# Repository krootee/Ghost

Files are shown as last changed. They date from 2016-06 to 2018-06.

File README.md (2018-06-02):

# Ghost32

## Summary

Ghost32 is an autonomous car used for Folkrace robot competition. It uses a customized Losi 1/24-scale RTR 4WD Rally Car, and with a custom created PCB and various sensors. The "brain" of the car is an ESP32, and it is programmed using C++ and Mongoose OS.

This GitHub repository contains all relevant info for creating both hardware and software.

//More details about the project can be found on http://scalpel78.github.io/Ghost/

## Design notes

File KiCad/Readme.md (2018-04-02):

# Custom PCBs for Ghost

### PCBs

The bottom board, the GhostESP32, contains primarily the ESP32, a micro USB, an MPU-9250 and connectors.

The top board, the GhostSensorboard, contains primarily connectors for all the sensors, servos, power, startmodule, etc.

In the first revision it used the "Sick of Beige" 50x50 formfactor, but in the second revision this has been reduced to the slightly smaller 60x37 formfactor. Also, in the second revision the accelerometer/gyro and compass has been moved from the top board to the bottom board.

The electronics use two boards that are connected together using a Hirose FX8C connector.

There is a KiCad footprint for the Hirose FX8C-60 pin connector at: https://github.com/librespacefoundation/lsf-kicad-libs
and Sick-of-beige layout from https://github.com/TomKeddie/openscad-scripts

#### PCB - GhostESP32 (Microcontroller)

- [x] ESP-WROOM-32
- [x] MicroUSB
- [x] USB-to-UART (CP2102)
- [x] Power LED
- [x] Reset buttons for ESP-WROOM-32 (Reset)
- [x] Accelerometer/Gyro/Compass (MPU-9250)
- [x] Temperature (TMP102)
- [x] Connector for ESC/Motor
- [x] Connector for Steering servo

##### PCB - GhostSensorboard (Sensors and connectors)

- [x] I2C multipexer (TCA9548ARGER, 2pcs)
- [x] 16 connectors for I2C/IR sensors
- [ ] RGB LED
- [x] Connector for Startmodule
- [x] 3V3->5V level shifter (BSS138, see Sparkfun)

### Rev 6 (future)

#### Changes from Rev 5 to Rev 6
- [ ] Fix schematic for Q2. Pins 2 and 3 are switched.
- [ ] Use Sick-of-beige 60x37
- [ ] Change footprint for the 100uF capacitors to a bigger one?
- [ ] CP2102, remove the resistors for D- and D+
- [ ] Make sure the capacitors for MPU9250, CP2102 and ESP32 as placed close to the chip.
- [ ] CP2102, Add 4.7k pullup resistor to 3V3 on RST pin
- [ ] Replace CP2102 with CP2102N (faster, pin compatible, might require two more resistors)
- [ ] Make the CP210N bus-powered. No need to power it except when programming via USB. 
(see https://www.silabs.com/documents/public/application-notes/an976-cp2102-3-4-9-to-cp2102n-porting-guide.pdf)
Add 22.1k and 47.5k voltage divider.
- [ ] Replace slide switch with side switch, f.inst: 131-6979
- [ ] Smaller 3V3 regulator. How much current do we draw at most?
- [ ] Ability to measure battery voltage. (LTC2943CDD, 2366039)
- [ ] Change resistors and capacitors 0402 to 0603.
- [ ] Fix footprint for TMP102 on Ghost Sensorboard

### Rev 5 (18.mar 2018)

Formfactor: Sick-of-beige 70x43

#### Notes and workarounds
- The Q2 schematic is wrong. Pins 2 and 3 are switched.

#### New/Changes
- [x] Fix footprint for TMP102. Was too big on Rev4.
- [-] Figure out why MPU9250 doesn't work on Rev4.
- [-] Test I2C and IR sensors on Rev4
- [-] Test the NanoPixels on Rev4
- [-] Test the Motor/ESC pwm and Steering PWM
- [x] Change to the slightly bigger TCA9548 chip for easier soldering?
- [x] Minor layout adjustments; Move Q1, Q2, R1, R2 between CP2102 and ESP32
- [x] Minor layout adjustments; Move R15 and C12 closer to SW1 switch
- [x] Remove the NanoPixels
- [x] Change I2C to use pins 21 (SDA) and 22 (SCL)
- [x] Changed I2C pullups from 2k2 to 10k
- [x] Change PCB outline to a rectangle with rounded corners
- [x] Change MPU9250 to use I2C addr 0x69, instead of 0x68

### Rev 4 (aug 2017)

Formfactor: ca 63x43mm with "drone arms"
Had wrong footprint for TMP102.

- [x] Replace MPU6050 and HMC5883 with a MPU9250
- [x] Remove the TX/RX leds and BSS138 opamps
- [x] Remove the FX8 connectors
- [x] Breakout more of the pins from ESP32 to headers
- [x] Add JTAG header for ESP32
- [x] All resistors and capacitors should use footprint 0402.
- [x] Simplified components around reset switch
- [x] ESD protection (Farnell: 238-3318)
- [x] USB resistors on D+ and D-
- [x] Temperature sensor (TMP102)

### Rev 3 (never built??)

### Rev 2 (mars 2017)

Used formfactor Sick-of-beige 60x37

### Rev 1 (feb 2017)

Used formfactor Sick-of-beige 50x50.

### Other

Sensor board:
- [x] Add 5V regulator to go from VBAT to +5V
- [ ] Is the button on Sensorboard tall enough? (And do we need it?)
- [ ] Add motor driver (MCP8063? DRV10970?)
- [x] Put an LED in each corner of the Ghost Sensorboard.
- [ ] TCA9548ARGER has wrong footprint. Needs one with thermal GND pad.
- [x] Connect battery directly to top board
- [x] Add on/off switch (MFP106D, 807527)
- [ ] Remove the IR receiver?
- [x] (alt: replace IR sensor with one in stock)
- [x] All resistors and capacitors should use footprint 0402
- [x] Add NeoPixel nano RGB leds
- [x] Remove 8 of the IR sensors connectors + one I2C mux to save space

PCB
- [ ] Move motor and steering connectors away from ESP32 on other board
- [x] Typo. Steering is mistakenly written as Start.
- [x] 6mm keepout around the mounting holes, see Sick of Beiges specs
- [x] Ground area used by U12+P3 is not connected to rest of board!
- [ ] 4-layer board
- [x] Make sure no GND plane under MPU-9250, see https://github.com/kriswiner/MPU9250/issues/43

### Others

Arduino code for the Startmodule-remote is here:
http://p1r.se/startmodule/implement-yourself/#comment-1271

------- OLD BELOW ----------

### Schematic

- [x] Startmodule pins are wrong order!! Should be VCC, GND, Start
- [x] Add two buttons for ESP-WROOM-32
- [x] Change to TCA9548ARGER (smaller footprint than TCA9548APWR)
- [x] Change from 0805 to 0603 size for capacitors, resistors and leds.
- [x] Remove extra PWM pins?
- [x] Change pin headers around so that pin 1 (the square) is GND
- [x] Use resistor array for IR sensor resistors
- [x] Red LED is always on. Figure out why. (was Q1 pins switched)
- [x] Change the Q1 transistor schematic component to use Q_NPN_BEC
- [x] Add 6 pin header for FTDI Basic, for programming ESP8266
- [ ] Remove LED strip connector?
- [ ] Add connectors to breakout ESP-WROOM-32 pins?
- [ ] Micro USB for programming ESP-WROOM-32s
- [ ] CP2102 (or similar USB-to-UART bridge)
- [ ] Use the new 47uF or 100uF alu caps?
- [ ] Use the new resistor networks?

##### Board/layout
- [ ] Current size is about 90mm x 63mm. Try to reduce to "Sick of Beige" size 80x49 or 70x43.
- [ ] Make sure I have four mountingholes for acrylic cover
- [ ] Startmodule header needs indicator for direction
- [ ] Put all pin headers on the border of the PCB
- [ ] Fix missing trace between R7 and D3(red)
- [ ] Move LEDs to a more visible place. They are under Teensy USB now.
- [ ] Move MPU-6050 to the center of the board.
- [ ] Make sure antenna part of ESP-WROOM-32 sticks outside board.

#### Car
- [X] Fix wireposition on steering servo
- [ ] Change the steering servo
- [ ] Mount wheel encoder
- [ ] Create mount for IR sensors
- [ ] Figure out which battery to use
- [ ] Mount new motor.
- [ ] Figure out the gears for the motor

#### Other
- [ ] Draw acrylic cover for PCB in OpenSCAD
- [ ] Laser-cut an acrylic cover for PCB
- [ ] Use 0.1 ohm 1% 2W current sense resistor for the INA219. Find part at Farnell.

## Bill of materials / Partlist

### RC car

## PCB Features

### Teensy 3.1/3.2 (external)

Uses a standard Teensy 3.2 board from pjrc.com.

The Teensy is based around a MK20DX256VLH7, an ARM Cortex-M4 at 72MHz. It contains 2k EEPROM where the car's configuration is stored.

In later versions I'm planning on incorporating a custom Teensy directly into the PCB. If so, then I can remove the MIC5219-3.3, since the Teensy also comes with a 3.3V regulator.

### HM-11 bluetooth

Revision 1 has both Bluetooth and WiFi. This version is for determining if BT or WiFi is easiest to work with. Later versions will only have one of the two.

It is not allowed to remotely control the car during the Folkrace, but the BT/WiFi functionality is very useful during debugging and experimentation. It allows receiving telemetry data during racing, and makes it easy to change configuration without reprogramming entire Teensy.

### ESP8266 WiFi

An ESP-12E.

The ESP8266 contains an 80MHz 32-bit RISC CPU with 16 GPIOs, SPI, UART and I2C. In itself it is a powerful chip, and could potentially make the Teensy redundant.

Information gathered from (http://www.esp8266.com/wiki/doku.php?id=esp8266-module-family).
Pin 1, RST: Connect to switch to GND in order to reset.
Pin 3, EN : Connect to 3.3V to enable.
Pin 8, VCC: To 3.3V
Pin 15,GND: To GND
Pin 16,GPIO15: Need to connect to GND.

### MPU-6050 (accelerometer and gyro)

In order to detect movement there is an MPU6050 MEMS motion tracking device with accelerometer and gyro, and an HMC5883 compass.

To interface the MPU-6050 I'm using code from Jeff Rowberg (https://github.com/jrowberg/i2cdevlib/tree/master/Arduino/MPU6050)

 Alternatively I'm going to use FreeIMU (http://www.varesano.net/projects/hardware/FreeIMU).

 Future revisions might replace this with a MPU-9250.

### HMC5883 (compass)

The compass is a slave-I2C device where the MPU-6050 is the master. FreeIMU uses these two components together.

### I2C multiplexer and 8 IR sensors

Since the I2C IR sensors I'm using all have the same I2C address I need to multiplex between them using an I2C mux.

The multiplexer is an TCA9548APWR with eight channels.
In Rev 1 I'm using a multiplexer with footprint TSSOP (7.8 x 4.4 mm). In future revisions I'm considering changing to TCA9548ARGER which has a VQFN footprint (4 x 4 mm). They both have 24 pins, but NOT the same pin configuration.

The IR sensors are eight Sharp GP2Y0E02B, which uses I2C. It has range 4-50cm.

### Current sensor

An INA219BIDR is used for sensing current usage. Measures current flow from the battery connected. Device is controlled by I2C. Adafruit has an Arduino library for the INA219.

The sensor can sense up to 3.2A in 0.8mA steps.

Arduino code: /Arduino/CurrentSensor/CurrentSensor.ino

### Voltage regulator

The 7.4V Li-Po battery is connected to the XC-10A ESC, and it provides regulated +5V/1A to the PCB. The Hobbyking XC-10A accepts from 3v-13V, so I could potentially use an 11.1V LiPo.

On the PCB is a MIC5219-3.3YM5 voltage regulator for providing 3.3V. It has a max output of 500mA.

The Teensy also has built in 3.3V regulator. It can supply 500mA. Currently not used.

### Toggle LEDs

There are two leds, one red and one green, which can be toggled from Teensy. Only one of them can be active at any given time.

When Teensy pin 2 is HIGH the transistor turns on, and the Green led lights up. When pin 2 is LOW the Red LED lights up.

NB, in Rev 1 the schematic part for the transistor is wrong. It has switched Collector and Emitter, leaving the red led on always. Fixed in Rev 2.

### GPIOs
#### Startmodule

For connecting a Startmodule from http://www.startmodule.com/.

NB - Rev 1 had wrong pinout! Fixed in Rev 2.

#### Steering servo

For controlling a SG-90 or similar microservo for steering. I'm using Losi part LOSB0814, which is a three-pin replacement servo with servo saver.

  1. PWM control signal to Teensy pin 4.
  2. +5V
  3. GND

#### Motor

A 3 pin header for connecting an Electronic Speed Control (ESC). I'm using the HobbyKing XC-10A esc.

  1. PWM control signal to Teensy pin 3.
  2. Power from the Li-Po battery. Used to power entire PCB.
  3. Ground

Arduino code: Arduino\MotorHobbykingXC10AESC\MotorHobbykingXC10AESC.ino

#### General purpose button

A generic purpose switch, usage to be determined by user. Use INPUT_PULLUP when setting pinMode(pin, INPUT_PULLUP).

#### General purpose PWM connector

Usage to be defined by user
  1. PWM control signal to Teensy pin 16.
  2. +5V
  3. GND

#### Wheel encoder

Either GP1A51HRJOOF or KTIR0611S photo interrupter. Used to measure rate of spinning for the main drive shaft.

## Current consumption

If I need more than 500mA on the 3.3V rail I might go for å AMS1117 or similar, which can handle 1A.

(todo)

## Further research

https://github.com/guyc/RC5
https://github.com/pinkeen/avr-rc5
http://clearwater.com.au/code/rc5

https://github.com/platisd/AndroidCar/

https://github.com/esp8266/Arduino/blob/master/doc/reference.md

http://control.ee.ethz.ch/index.cgi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

Check out the USB driver chip CH340.

https://esp-idf.readthedocs.io/

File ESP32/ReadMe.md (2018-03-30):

# ESP32 / ESP-WROOM-32

This page contains my notes about programming the ESP-WROOM-32 module.

The primary sourcecode for the Ghost-folkracer car is in the /Folkracer directory.
All code for testing individual parts of the car can be found in the /TestPrograms dir.

## Using Arduino IDE

To program the board using the Arduino IDE first follow the installation instructions at https://github.com/espressif/arduino-esp32.

In Arduino IDE choose the board called 'ESP32 Dev Module'.
The blinky-led is on pin 23.

## Using C++ and ESP-IDF

Documentation and installation guide for ESP-IDF can be found at: https://esp-idf.readthedocs.io

### Prerequisites (Ubuntu/Linux Mint)

Perform installation Step 0 to Step 2 from the documentation link above.

In addition, add this to ~/.bashrc as well (from Step 4):

    export IDF_PATH=~/esp/esp-idf

### Flashing

Go to the /Ghost/ESP32/Folkracer directory, and run

    make flash (flashes app, bootloader and partition table)

or

    make app-flash (flashes just the app)

or

    make all flash monitor (builds everything, flashes and starts the monitor with one command)

To close the 'monitor' use keys Ctrl+] (which is Ctrl+AltGr+9 on Norwegian keyboards).

### Performance

    make -j5 (performs the build with parallell threads)

### Configuring Eclipse

When starting Eclipse, set ~/GIT/Ghost/ESP32 as the workspace folder.

On properties for the project, go to "C/C++ Build", and uncheck "Use default build command".
Go to Environment, and add IDF_PATH = ~/esp/esp-idf
Go to "C/C++ General"->"Paths and Symbols", select "GNU C", click Add..., and add these:

    ${IDF_PATH}/components/esp32/include
    ${IDF_PATH}/components/newlib/include
    ${IDF_PATH}/components/freertos/include
    ${IDF_PATH}/components/nvs_flash/include
    ${IDF_PATH}/components/driver/include
    ${IDF_PATH}/components/log/include

and lastly

    /myapp/build/include (with the "Is a workspace path" checkbox ticked, and correct appname)

### Using OTA

First, make sure the ota.bin firmware has been deployed using USB cable.

    cd ~/esp/esp-idf/examples/system/ota
    make menuconfig
        configure correct SSID, password, IP to webserver, and .bin file to download.
    make flash

Set up a local HTTP webserver in the /build directory of the application to deploy Using

    python2 -m SimpleHTTPServer 8070

Now, rebuild the project we want to deploy, so that the .bin file gets created/updated.
Press Reset button on ESP to make it restart, download new image and reflash itself.

### Connecting serial

Install Minicom

    sudo apt-get install minicom

and to use

    minicom --device /dev/ttyUSB0

or you can use

    make monitor

Quit it using Ctrl+] (which is Ctrl+AltGr+9)

### Troubleshooting

##### Unable to flash via USB - permission denied

When running "make app-flash" or similar you get error saying permission denied to the USB device.

This can be fixed by adding the current Linux-user to the 'dialout' group.

    sudo usermod -a -G dialout $USER

Reboot the machine afterwards.

##### OTA fails
https://github.com/espressif/esp-idf/issues/231

##### TODO

- separate task_actuators into task_motor and task_steering, and write to two separate queues from task_drivecomputer.

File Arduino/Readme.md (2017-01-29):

# Arduino code

### Isolated sketches for testing

Most of the code in this directory are small Arduino sketches focused on just testing and verifying one particular piece of the puzzle. There is one for the IR sensors, one for the motors, one for the startmodule etc. This makes it easy to validate that a particular piece of hardware works.

### Main program

The code in the Ghost folder is the main program for the RC car. It contains the full program for running the RC car.

### Path planning

Middle Path (MP) and Minimum Curvature Path (MCP) - see http://www.aueb.gr/users/ion/docs/stavrinos_bsc_thesis.pdf

##### Further research

D* lite

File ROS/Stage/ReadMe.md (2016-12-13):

## Using Player/Stage to simulate

These files are used by Player/Stage to run robot simulation.

### Install

On Ubuntu 16.04 install ROS using ´´´sudo apt-get install ros-kinetic-desktop-full´´´. That should also bring in the ros-kinetic-stage application.

You _might_ need to add this to ~.bashrc

export LD_LIBRARY_PATH=/usr/local/lib64:$LD_LIBRARY_PATH}
export PKG_CONFIG_PATH=/usr/local/lib64/pkgconfig:$PKG_CONFIG_PATH}

Then start simulation by running

´´´stage gothenburg.world´´´

NB - I was unable to get Player working on Ubuntu 16.04. I tried downloading the current snapshot from https://sourceforge.net/p/playerstage/svn/HEAD/tree/, and built it, but never managed to get everything working.

### Links
http://rtv.github.io/Stage/
and
http://playerstage.sourceforge.net/index.php?src=stage
and
http://player-stage-manual.readthedocs.io/

http://askubuntu.com/questions/859110/install-package-robot-player-on-ubuntu-16-04

http://answers.ros.org/question/249570/gazebo-or-rviz/

https://discourse.ros.org/t/using-ros-for-simulating-autonomous-rc-cars/924

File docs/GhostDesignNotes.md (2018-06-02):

# Ghost Design Notes

*These design notes are scribbled down as I'm doing research for my autonomous Folkrace cars.*

*I'm trying out several different options for the software, so there are code for both Arduino, FreeRTOS and Mongoose OS. The last one is my main focus now.

## Sensors

* Either up to 8 or up to 16 distance sensors. Hopefully 8 will be enough.
* Compass
* Accelerometer/Gyro
* Wheel encoder

___
## Logic

The math in the car will use Vectors as the main means of calculations. 
Each distance sensor is one vector where the direction is constant (set by how it is mounted on the car), and a variable amplitude (the distance measured). 

By combining two vectors pointing to the same side wall, the angle of the car vs the wall can be calculated using vector math.

In addition, I'll use a vector to describe the desired forward motion. The vector will indicate the direction and speed the car should go.

The speed of the car will be affected by the steering angle. When going straight forward the car will move at a higher speed, than when turning. A sharp turn should be done at a very low speed.

The minimal speed the car can go must be identified.

Using a sensor to measure the rotation of the driveshaft, Odometry can be used.

### Car and sensorssetup

Each sensor will have a constant offset from a common point of the car, describing how far in the X and Y direction the sensor is from the zero-point.

The Zero-point is in the middle between the two rear tires.

The Tread-size is the distance between the two rear wheels, and the Wheelbase is the distance between the rear and front wheels. [1]

Overall car state:

```
{
  env: {
    leftwalll: 32,
    rightwall: 29,
    incline: 3
  },
  pose: {
    velocity: 180,
    direction: 230,
    steering: 76,
    motorspeed: 102,
    odometer: 79
  },
  sensors: {
    irsensor1: true,
    irsensor2: true,
    irsensor3: true,
    irsensor4: false,
    irsensor5: true,
    odometer: true,
    compass: true,
    startmodule: true,
    accelerometer: true
  }
}
```

The modes can be: 'waiting', 'driving', 'stopped'.

Heading is degrees in [0-360].

Speed is in centimeters pr second. It is the actual speed, not the desired speed.
___

## Sensor Fusion

## Math
For Matrix math - http://arma.sourceforge.net. Remains to figure out how to use it from ESP32.

https://www.sciencedirect.com/science/article/pii/S1877050917301473

# Sources
[1] https://www.youtube.com/watch?v=i6uBwudwA5o

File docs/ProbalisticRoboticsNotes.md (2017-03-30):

# Notes from Probabilistic Robotics book
Book authors: Sebastian Thrun, Wolfram Burgard, Dieter Fox

Notes: Frode Lillerud, march/april 2017

# Chap 1 - Basics

### 1.3
Probabilistic robotics tend to be more robust than model-based motion planning techniques or reactive behavior-based approaches.

(My Arduino based folkracer is mostly "reactive behavior based", since it just reacts to the IR sensor inputs.)

Probabilistic robotics is have weaker requirements on the accuracy of the robot's model, and the accuracy of the sensors.

Two disadvantages are that PR have a higher *computational complexity*, and there is *a need to approximate*.

# Chap 2 - Recursive State Estimation

### 2.1

At the core of PR is the idea of *estimating state from sensor data*. State estimation seeks to recover state variables from the data.

### 2.2
``p(X=x)`` where X is the discrete set of all possible values, and x  is a specific value. This is commonly abbreviated as p(x).

#### 2.3.1 - State

State is denoted by ``x``, and ``xt`` is the state at time t.

Pose: Location and orientation relative to a global coordinate frame. Pose includes variables for the *configuration of the robots actuators*.

Robot *velocity* and *the joints velocities* are commonly referred to as *dynamic state*.

#### 2.3.2 - Environment Interaction

*Environment measurement data* is information gathered via cameras, sensors, etc.

*Control data* can be *velocity*.

Measurement and control; Measurement gives the robot MORE information about the environment, while control (moving actuators etc.) leaves the robot with LESS information about the environment.

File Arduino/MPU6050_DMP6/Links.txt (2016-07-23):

http://diyhacking.com/arduino-mpu-6050-imu-sensor-tutorial/

https://github.com/jrowberg/i2cdevlib/tree/master/Arduino/MPU6050

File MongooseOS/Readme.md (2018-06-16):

# Mongoose OS

See https://www.mongoose-os.com and https://forum.mongoose-os.com

## Setting up programming environment

### Basic - getting started
    1) Download mos.exe into f.instance C:\MOS
    2) Put that directory into PATH
    3) Create a project folder

      cd MOS
      mkdir MOSprojectABC
      cd MOSprojectABC
      mos init

    4) In mos.yml, add the following line

      platform: esp32

    5) After making changes to the generated src/main.c file use this to build and flash to board.

      mos build
      mos flash
      mos console

    6) Connect to WIFI using

      mos wifi SSID password

Note; for Ghost32 PCB revisions 1-5 the maximum baudrate when flashing is 921600bps (from CP2102).
Planning to use CP2102N in revision 6+, which will give maximum baudrate 3Mbps.

      mos build --clean | grep "error"
      mos flash --esp-baud-rate 921600
      mos console

### Using Visual Studio Code
Once you've got the basic setup above working you should also consider configuring VS.CODE to have a better programming experience.

    1) Install Visual Studio Code
    Go to https://code.visualstudio.com

    2) Add the C/C++ extension
    3) Add the tasks.json file below:

    (content of tasks.json):
    {
    "version": "0.1.0",
    "command": "mos",
    "args": ["build"],
    "problemMatcher": {
        "owner": "cpp",
        "fileLocation": ["relative", "${workspaceRoot}"],
        "pattern": {
            "regexp": "^(.*):(\\d+):(\\d+):\\s+(warning|error):\\s+(.*)$",
            "file": 1,
            "line": 2,
            "column": 3,
            "severity": 4,
            "message": 5
        }
      }
    }

    4) Clone the GIT repository (to get the headers for intellisense)

    cd C:\MOS
    git clone https://github.com/cesanta/mongoose-os.git

    5) Add Include Dirs in VS.CODE

    In your main.c file, click on one of the "#include" lines that have a red squiggly underneath. Then click yellow lightbulb to the left, and choose "Add include path to settings".

    Under the Win32 section in the c_cpp_properties.json file that appears, add "C:/MOS/mongoose-os" to both "includePath", and to "path". Notice that it uses forward slash.

    Go back to main.c and observe that the red squiggly lines are gone. Type in f.instance 'mgos_gpio' to observe that you have intellisense now.

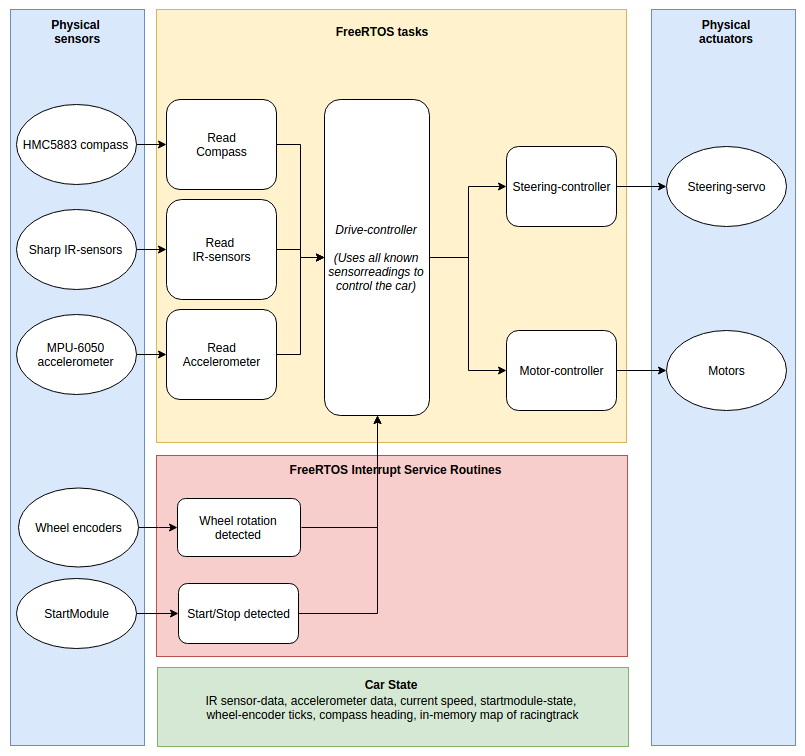
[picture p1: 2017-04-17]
docs/Architecture.png

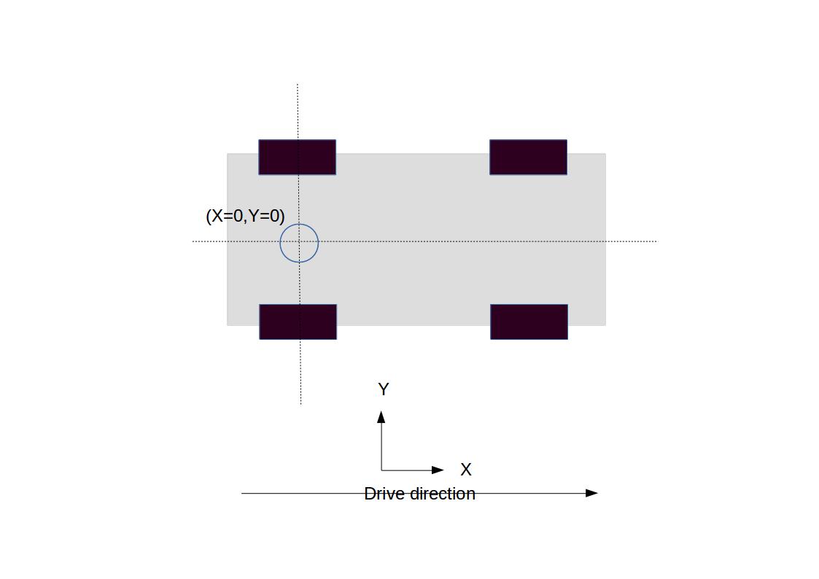
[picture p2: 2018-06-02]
docs/CoordinateSystem.jpg

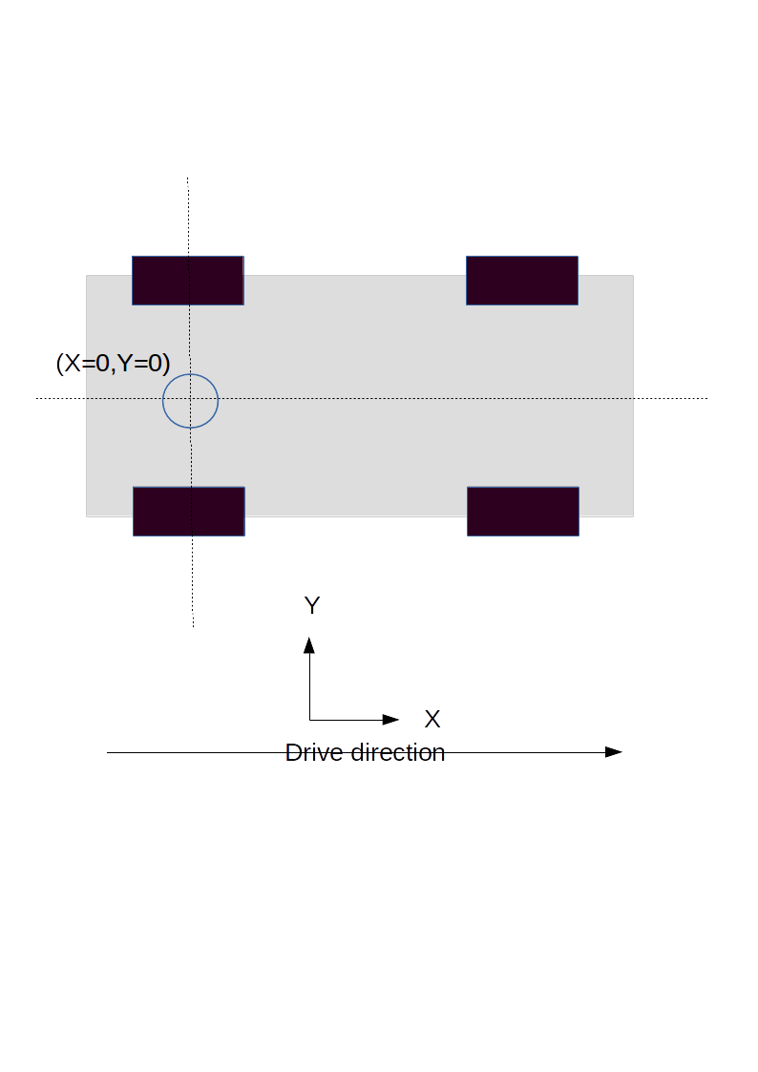
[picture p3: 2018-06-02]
docs/CoordinateSystem.png

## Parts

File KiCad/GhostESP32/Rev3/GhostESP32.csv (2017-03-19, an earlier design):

Id | Designator | Package | Quantity | Designation | Supplier and ref
1 | SW1 | SlideSwitchSpringReturn | 1 | SW_SPDT
2 | C1,C2,C3,C7 | C_0603 | 4 | 10uF
3 | C4 | C_0603 | 1 | 100uF
4 | C5,C8,C11 | C_0603 | 3 | 0.1uF
5 | C6 | C_0603 | 1 | 1uF
6 | C9,C10 | C_0603 | 2 | 1nF
7 | D1 | LED_0603 | 1 | RED LED
8 | D2 | LED_0603 | 1 | LED
9 | D3 | LED_0603 | 1 | RXLED
10 | D4 | LED_0603 | 1 | TXLED
11 | D5 | D_SMA_Standard | 1 | SSA33L Schottky
12 | J1 | hrs-fx8c-40p-sv | 1 | CONN_02X20
13 | P1 | USB_Micro-B | 1 | USB_OTG
14 | Q1,Q2,Q3 | SOT-23 | 3 | Q_NPN_BEC
15 | R1 | R_0603 | 1 | 2K
16 | R2 | R_0603 | 1 | 390
17 | R3,R4,R11 | R_0603 | 3 | 12K
18 | R5,R6 | R_0603 | 2 | 1k
19 | R7,R10 | R_0603 | 2 | 470
20 | U1 | SOIC-8_3.9x4.9mm_Pitch1.27mm | 1 | LM358
21 | U2 | SOT-223-3Lead_TabPin2 | 1 | NCP1117ST33T3G
22 | U3 | QFN-28-1EP_5x5mm_Pitch0.5mm | 1 | CP2102
23 | U4 | ESP32-WROOM | 1 | ESP-WROOM-32
24 | C12 | C_0603 | 1 | 10nF
25 | C13 | C_0603 | 1 | 2.2nF
26 | C14 | C_0603 | 1 | 0.22uF
27 | C15 | C_0603 | 1 | 4.7uF
28 | R8,R9 | R_0603 | 2 | 2k2
29 | U5 | QFN-24-1EP_4x4mm_Pitch0.5mm | 1 | MPU-6050
30 | U6 | QFN-16-1EP_3x3mm_Pitch0.5mm | 1 | HMC5883
31 | R12 | R_0603 | 1 | 10k

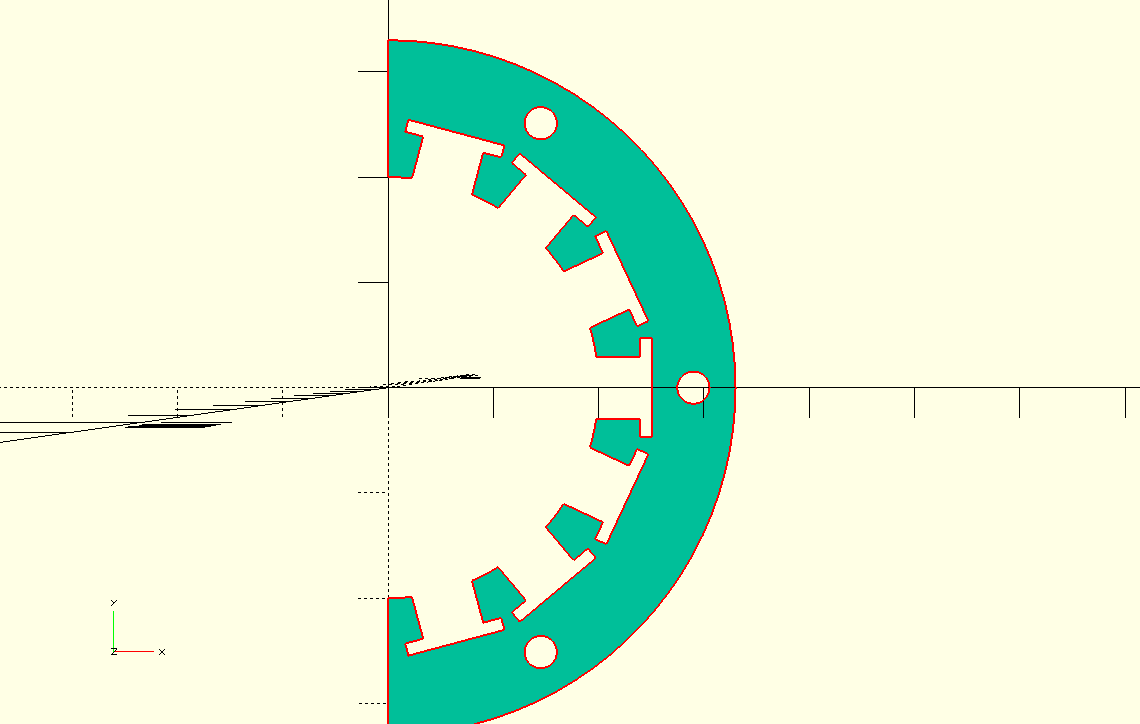
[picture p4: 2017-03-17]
Parts Lasercut/SensorFrame_WithHoles.png

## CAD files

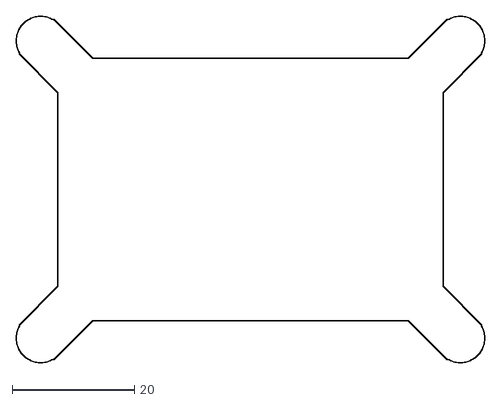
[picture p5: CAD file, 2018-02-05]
KiCad/OpenSCAD PCB/PCB-outline-rev4.dxf
76.7 x 56.7

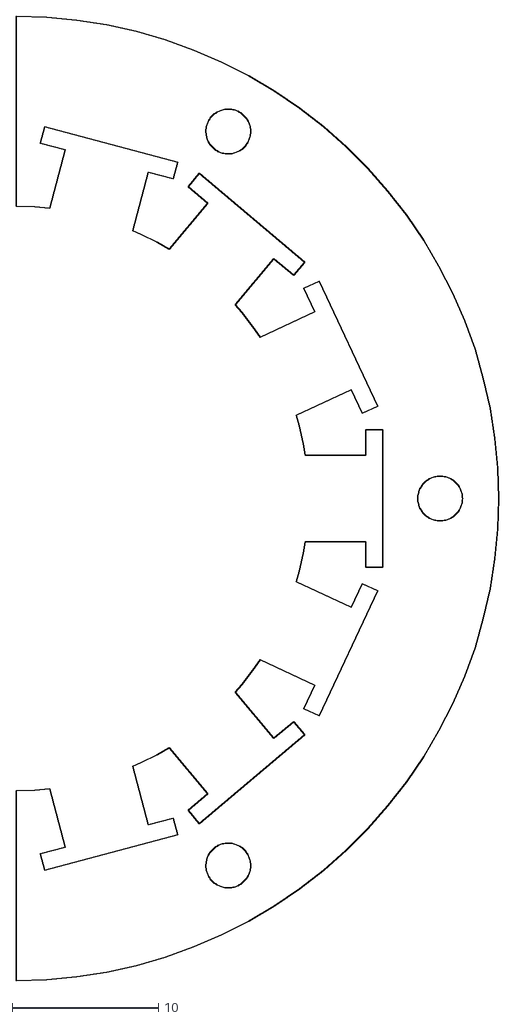
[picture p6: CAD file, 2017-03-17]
Parts Lasercut/SensorFrame_WithHolesV2.dxf
33.0 x 66.0

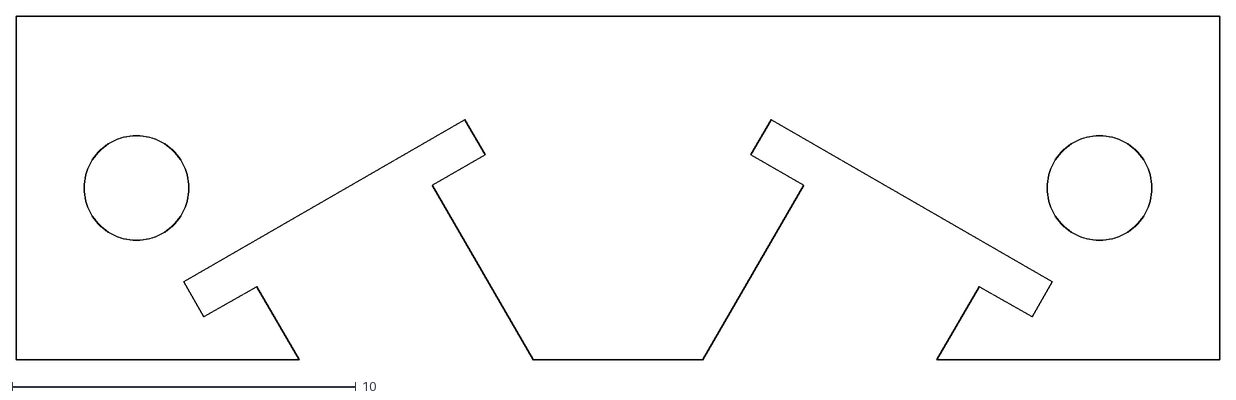
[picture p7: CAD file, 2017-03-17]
Parts Lasercut/MiniSensorHolder.dxf
35.0 x 10.0

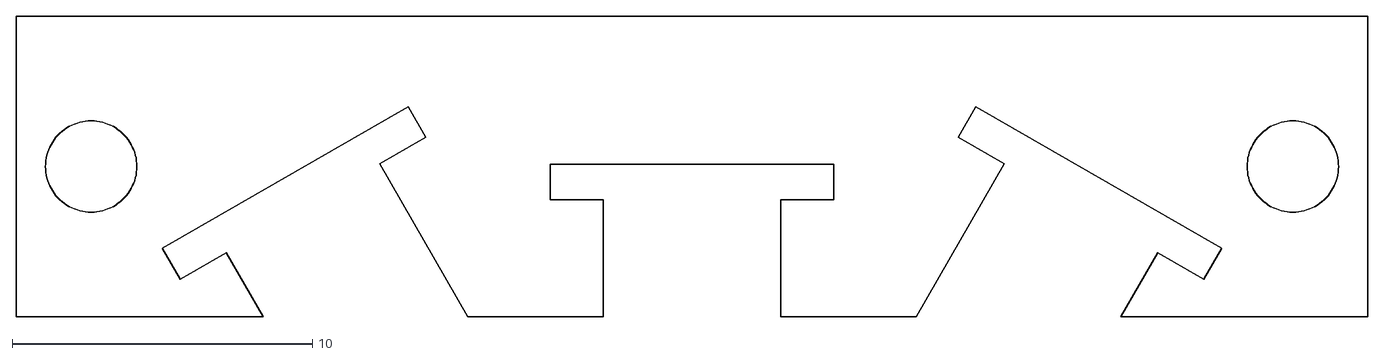
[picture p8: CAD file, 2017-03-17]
Parts Lasercut/ThreeSensors.dxf
45.0 x 10.0

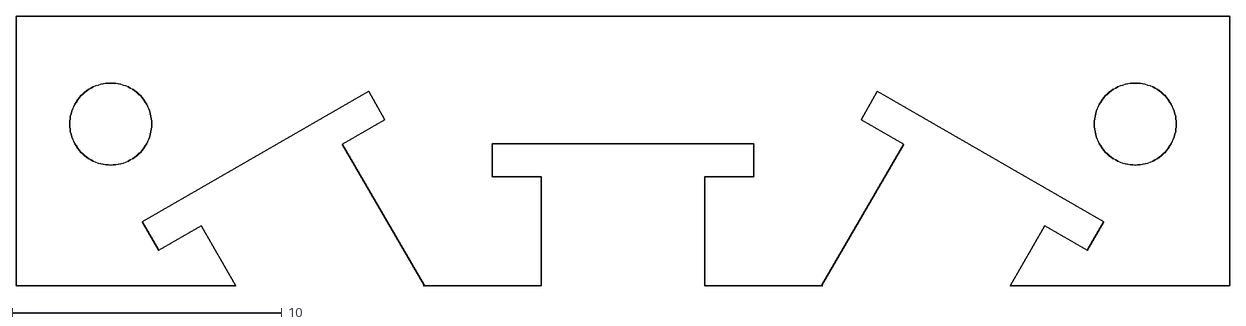
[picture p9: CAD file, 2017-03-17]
Parts Lasercut/ThreeSensorsV2.dxf
45.0 x 10.0

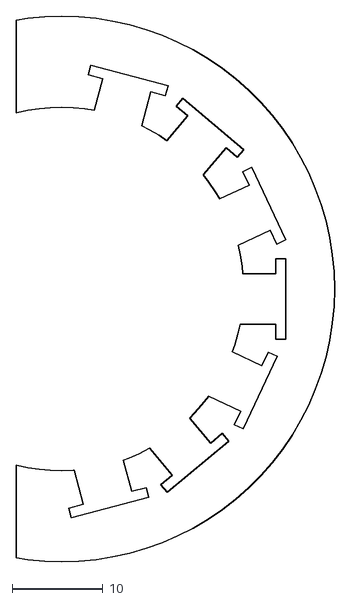
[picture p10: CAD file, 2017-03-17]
Parts Lasercut/SensorFrame.dxf
35.0 x 60.0

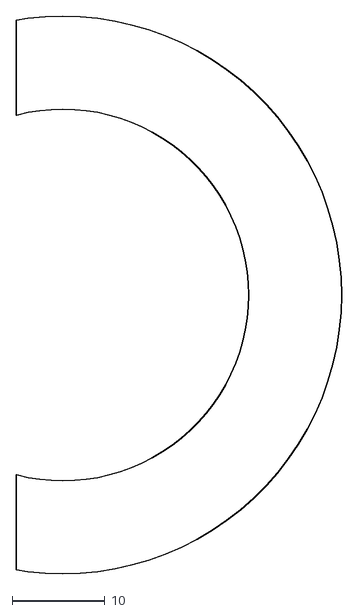
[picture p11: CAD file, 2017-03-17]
Parts Lasercut/SensorFrame_withoutHoles.dxf
35.0 x 60.0

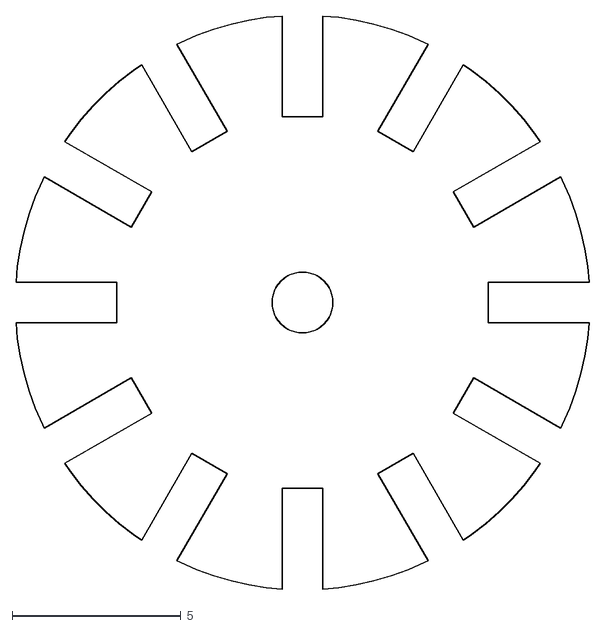
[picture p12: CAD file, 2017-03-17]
Parts Lasercut/EncoderDisc.dxf
17.0 x 17.0

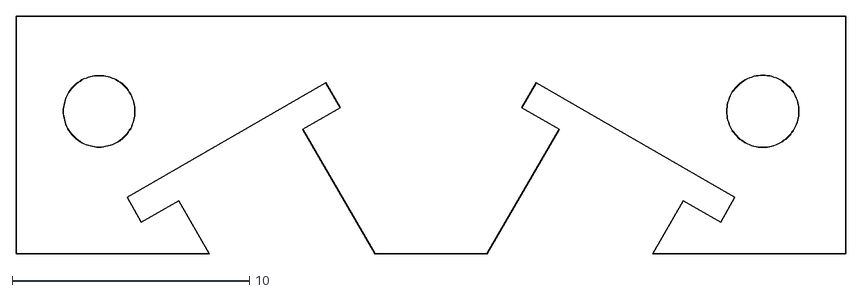
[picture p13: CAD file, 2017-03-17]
Parts Lasercut/MiniSensorHolderV2.dxf
35.0 x 10.0

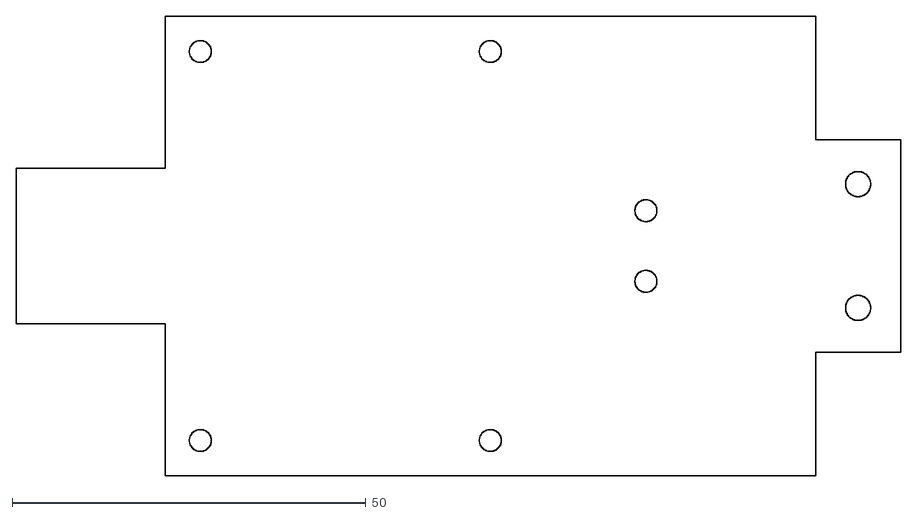
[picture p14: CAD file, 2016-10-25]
Parts Lasercut/PCB-mount.dxf
125.0 x 65.0

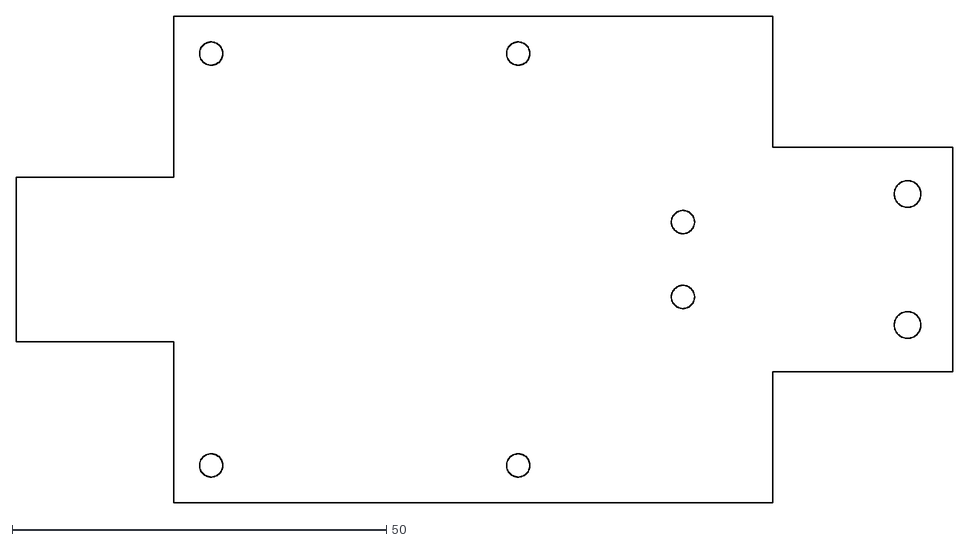
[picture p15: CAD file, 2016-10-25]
Parts Lasercut/PCB-mount-v2.dxf
125.0 x 65.0

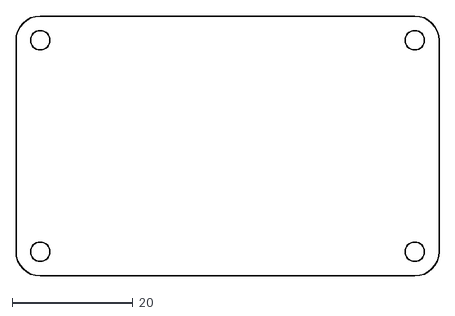
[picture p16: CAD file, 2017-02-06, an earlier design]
KiCad/GhostESP32/Rev3/DP7043.dxf
70.0 x 43.0

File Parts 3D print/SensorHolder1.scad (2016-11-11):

union() {
    linear_extrude(height=20) 
    {
        translate([0,0,0]) square([10,5]);
        translate([0,0,0]) rotate(90) square([15,5]);
        translate([45,15,0]) rotate(90) square([5,50]);
        translate([45,0,0]) square([5,20]);
        translate([35, 0,0]) square([10,5]);
    }
    translate([-10,-20,0]) cube([65,40,2]);
    #cylinder(size=20, height=20);
}

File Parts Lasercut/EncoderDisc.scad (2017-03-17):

$fn = 100;

projection(cut=false)
difference() {
    
    translate([0,0,0.5]) cylinder(r = 8.5, h=0.1);
    cylinder(r=0.9);
    for (a = [0 : 30 : 360])
        rotate(a) translate([7, 0, 1]) cube([3,1.2,1], center=true); //cylinder(r=0.8);
}

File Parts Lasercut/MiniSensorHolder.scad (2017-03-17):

$fn=100;

module sensor()
{
    width = 8;
    scaleFactor = 1.21;
    
    scale(scaleFactor)
    translate([0,-2.5,-5])
    union() {
        cube([5.5,5,10]);
        translate([5,-1.5,-3]) cube([1,width,19]);
    }
}


projection(cut=false)
difference() 
{
    cube([35, 10, 3], center=true);
    translate([5,-6.5,0]) rotate(60) sensor();
    mirror() translate([5,-6.5,0]) rotate(60) sensor();
    //translate([-5, -6.5, 0]) rotate(120) sensor();
    
    translate([14,1,-2]) cylinder(r=1.52, h=10);
    mirror() translate([14,1,-2]) cylinder(r=1.51, h=10);
}

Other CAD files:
Parts Lasercut/SensorFrame.scad
KiCad/OpenSCAD PCB/PCB-outline-rev4.scad
Parts Lasercut/PCB-mount.scad
Parts Lasercut/PCB-top-plate.scad
Parts Lasercut/ThreeSensors.scad

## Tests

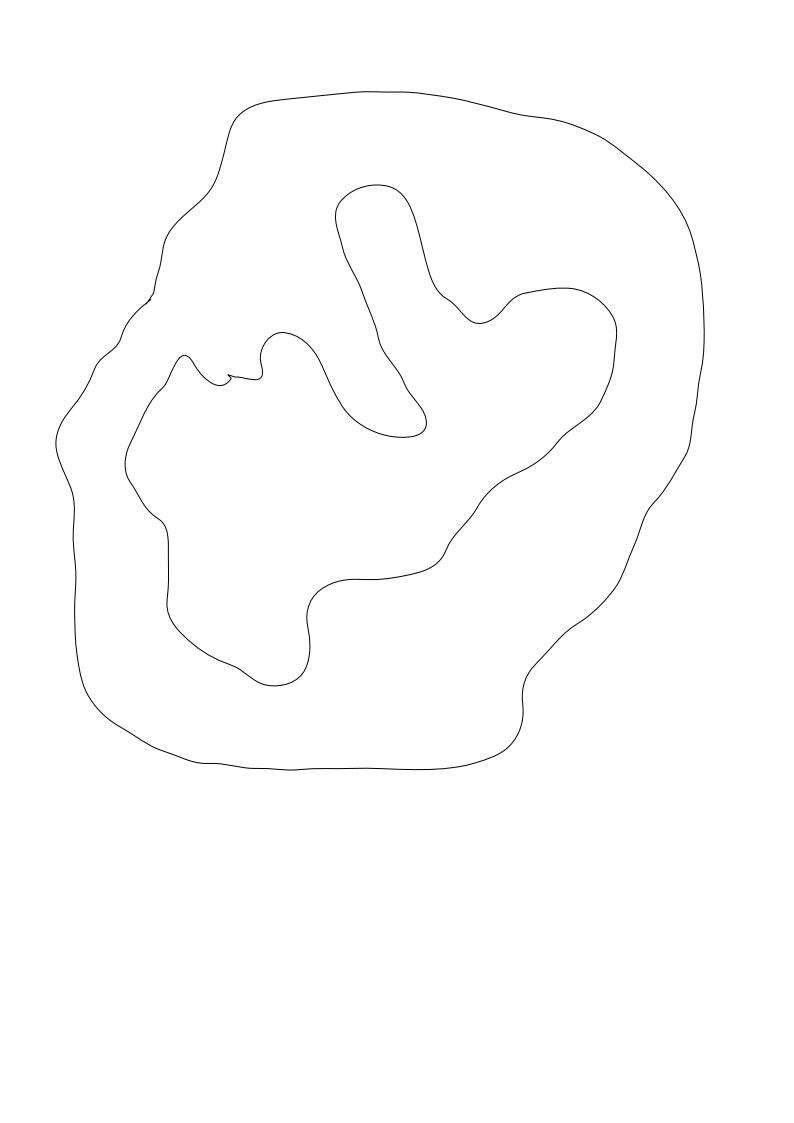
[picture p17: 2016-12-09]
ROS/Stage/bitmaps/test.bmp

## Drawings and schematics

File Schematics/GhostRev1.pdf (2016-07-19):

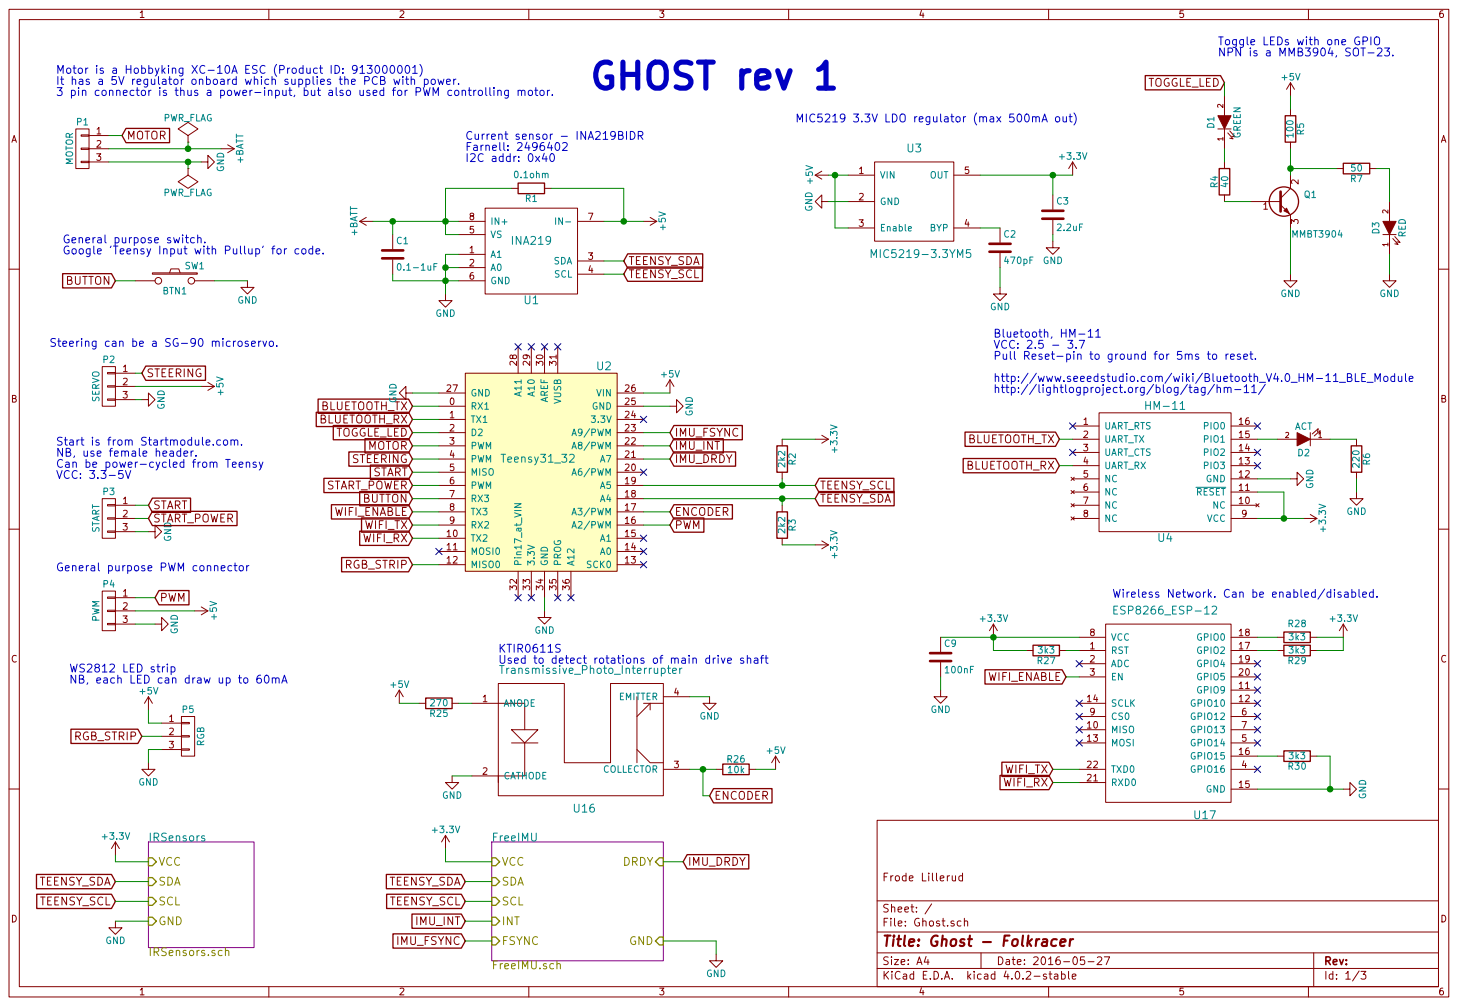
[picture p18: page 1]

Toggle LEDs with one GPIO

Motor is a Hobbyking XC-10A ESC (Product ID: 913000001)
It has a 5V regulator onboard which supplies the PCB with power.
3 pin connector is thus a power-input, but also used for PWM controlling motor.

MIC5219 3.3V LDO regulator (max 500mA out) +5V GND

General purpose switch.
Google 'Teensy Input with Pullup' for code. GND
GND WS2812 LED strip
BUTTON

Bluetooth, HM-11
VCC: 2.5 - 3.7
Pull Reset-pin to ground for 5ms to reset.
http://www.seeedstudio.com/wiki/Bluetooth_V4.0_HM-11_BLE_Module

Steering can be a SG-90 microservo.

Start is from Startmodule.com.
NB, use female header.
Can be power-cycled from Teensy

NB, each LED can draw up to 60mA

Id: 1/3 Title: Ghost - Folkracer File: Ghost.sch Sheet: / Frode Lillerud FreeIMU
FreeIMU.sch VCC
SDA
SCL
INT

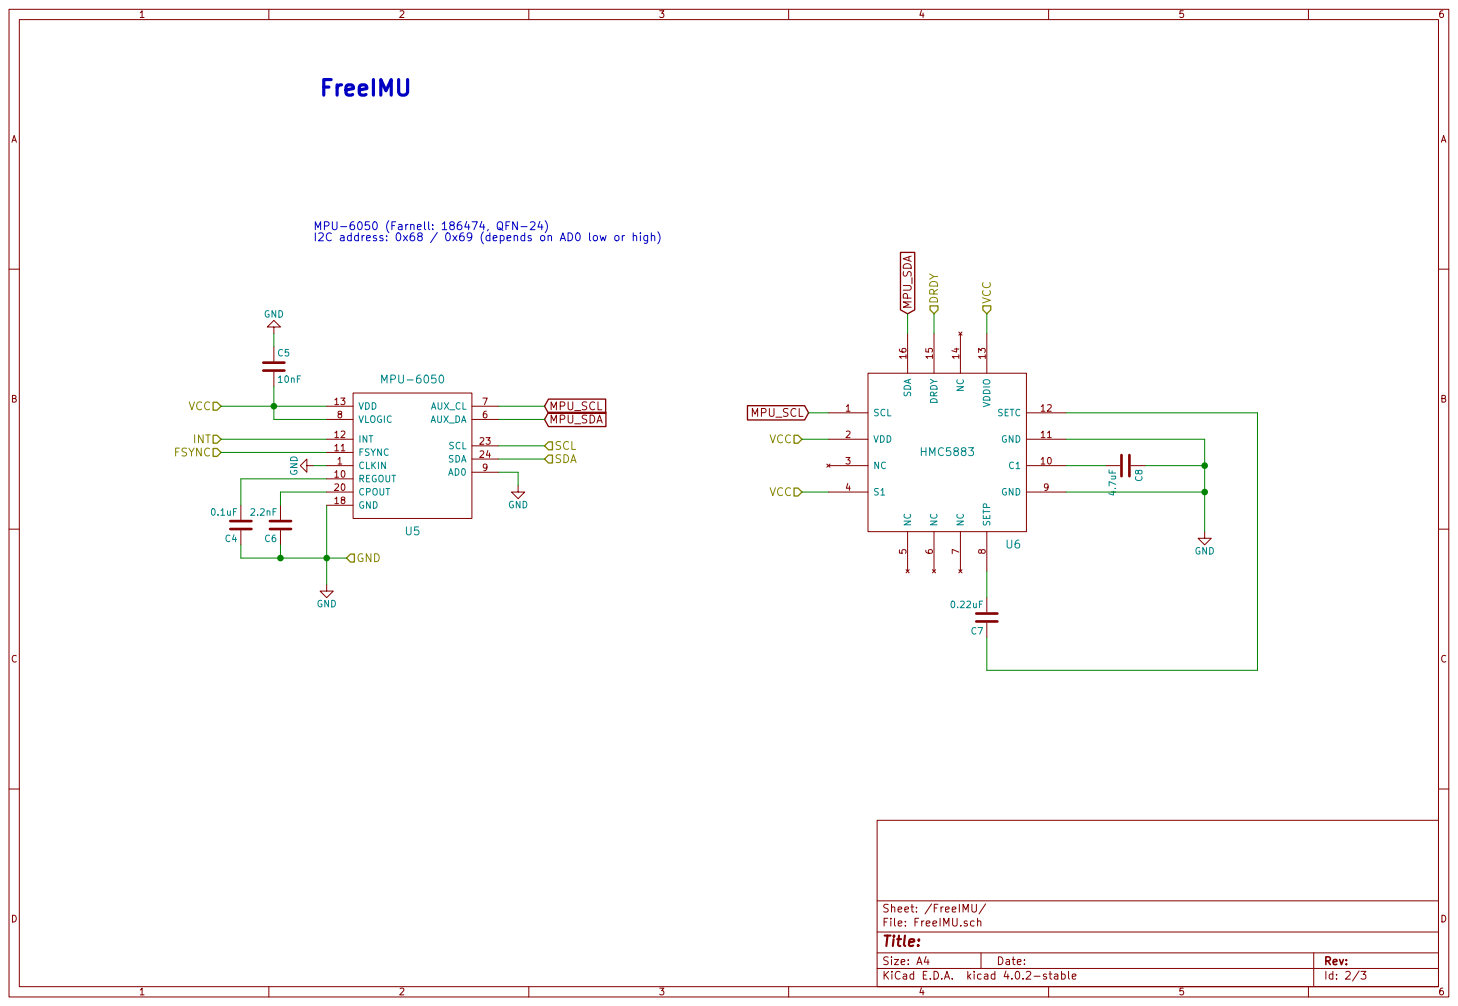
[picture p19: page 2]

MPU-6050 (Farnell: 186474, QFN-24)
I2C address: 0x68 / 0x69 (depends on AD0 low or high)

8 GND 9 C1 10 GND 11 SETC 12 VDDIO 13 NC 14 DRDY 15 SDA 16 U6 HMC5883

Id: 2/3 Title: File: FreeIMU.sch Sheet: /FreeIMU/

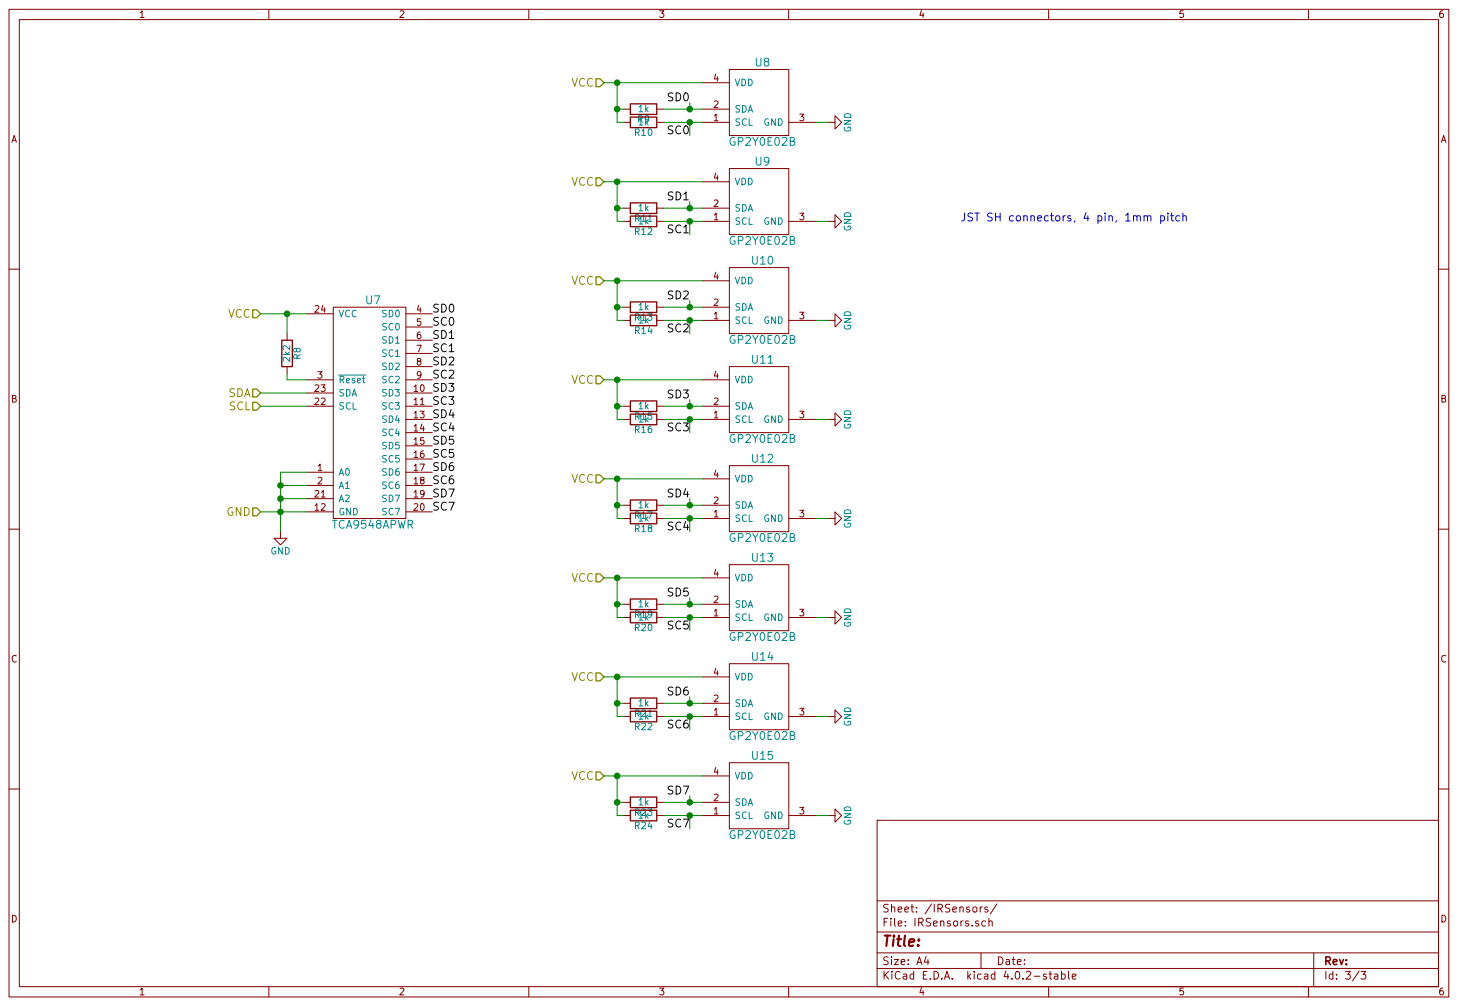
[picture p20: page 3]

JST SH connectors, 4 pin, 1mm pitch

Id: 3/3 Title: File: IRSensors.sch Sheet: /IRSensors/

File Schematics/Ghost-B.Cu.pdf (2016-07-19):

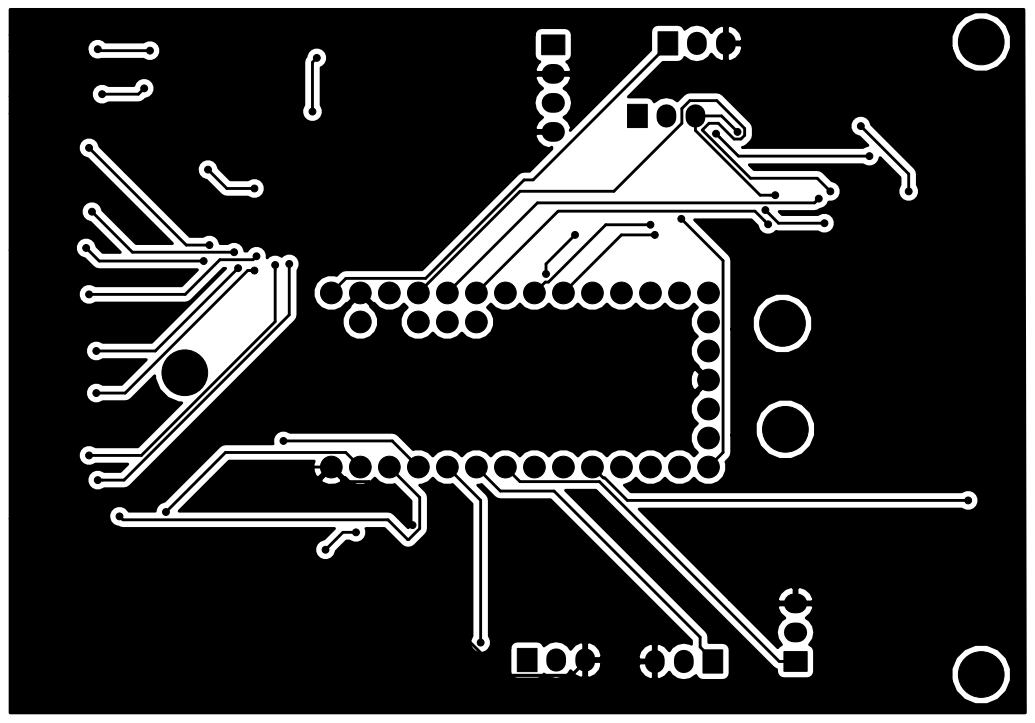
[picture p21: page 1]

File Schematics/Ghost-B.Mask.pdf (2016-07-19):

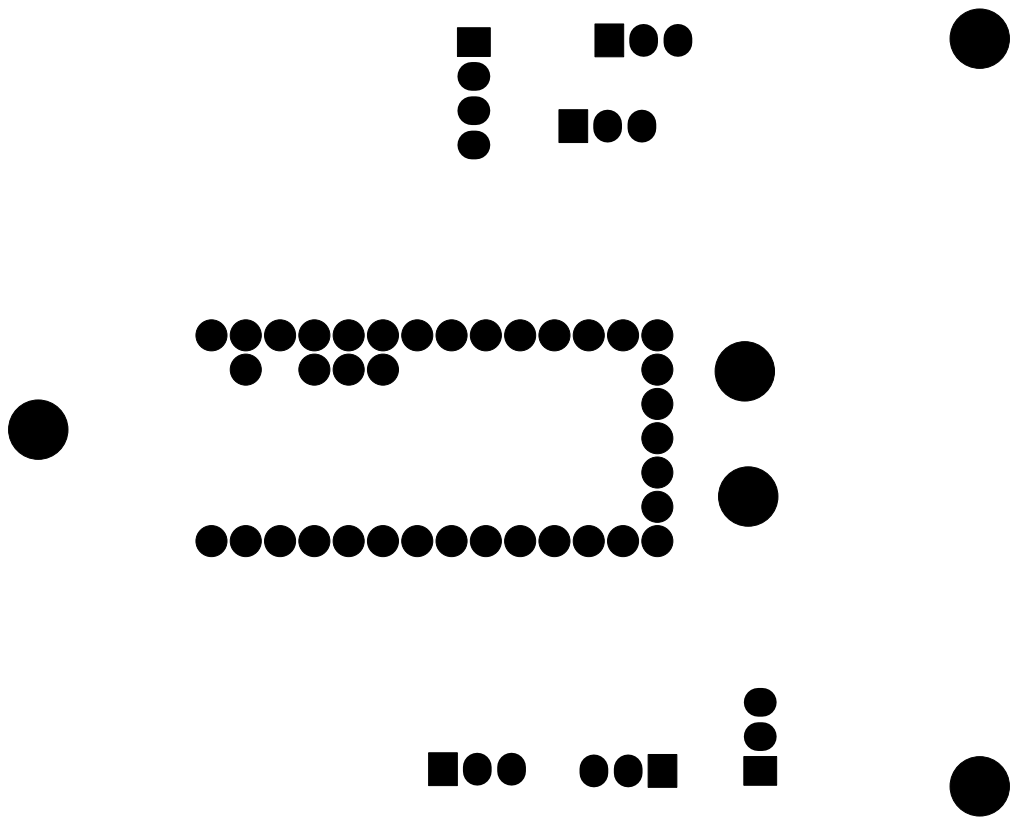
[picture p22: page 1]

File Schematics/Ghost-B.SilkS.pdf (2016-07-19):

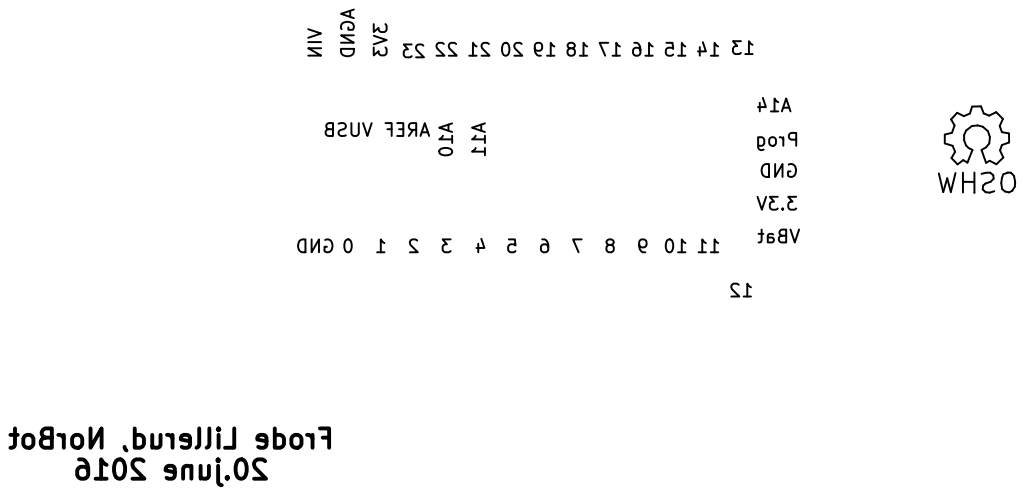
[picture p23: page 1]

20.june 2016 A10 A11VUSB AREF VIN AGND 3V3

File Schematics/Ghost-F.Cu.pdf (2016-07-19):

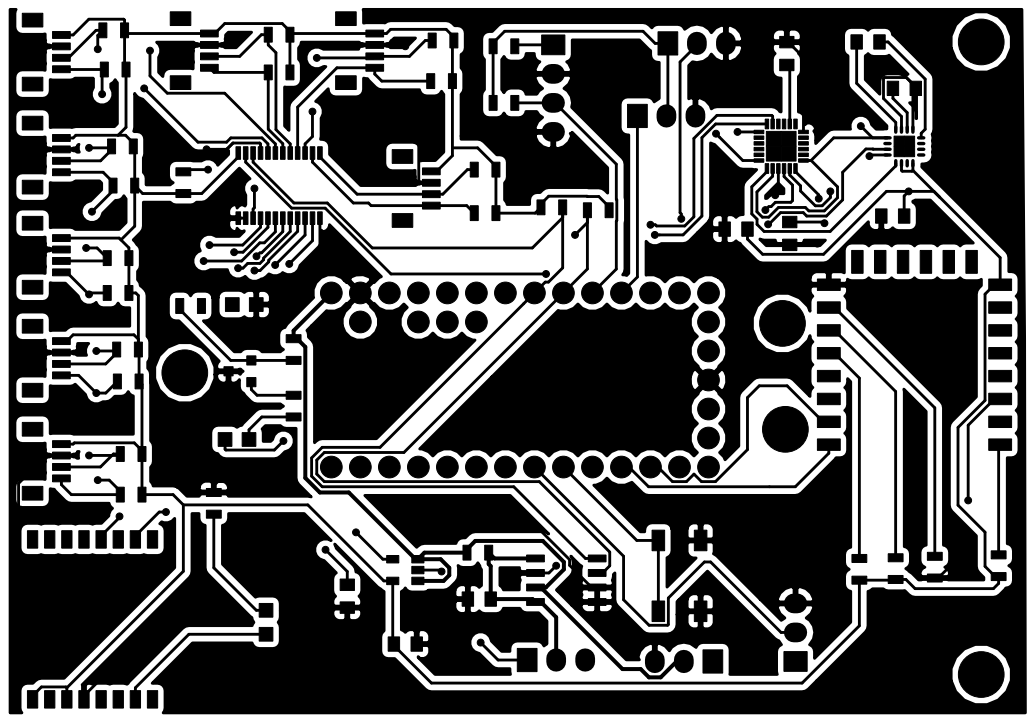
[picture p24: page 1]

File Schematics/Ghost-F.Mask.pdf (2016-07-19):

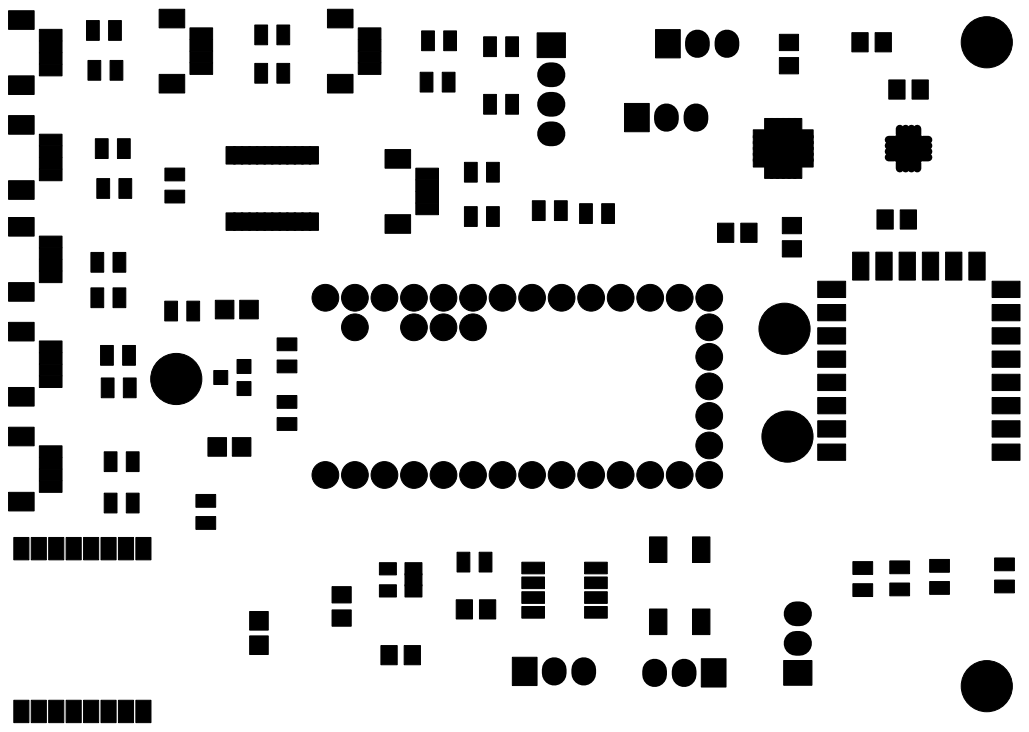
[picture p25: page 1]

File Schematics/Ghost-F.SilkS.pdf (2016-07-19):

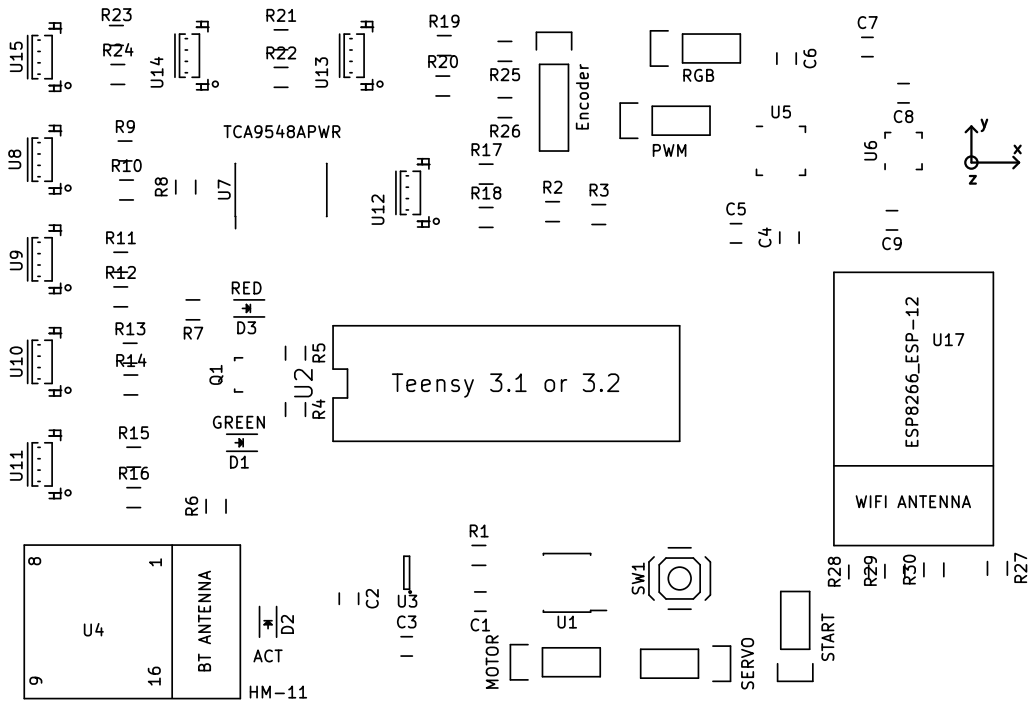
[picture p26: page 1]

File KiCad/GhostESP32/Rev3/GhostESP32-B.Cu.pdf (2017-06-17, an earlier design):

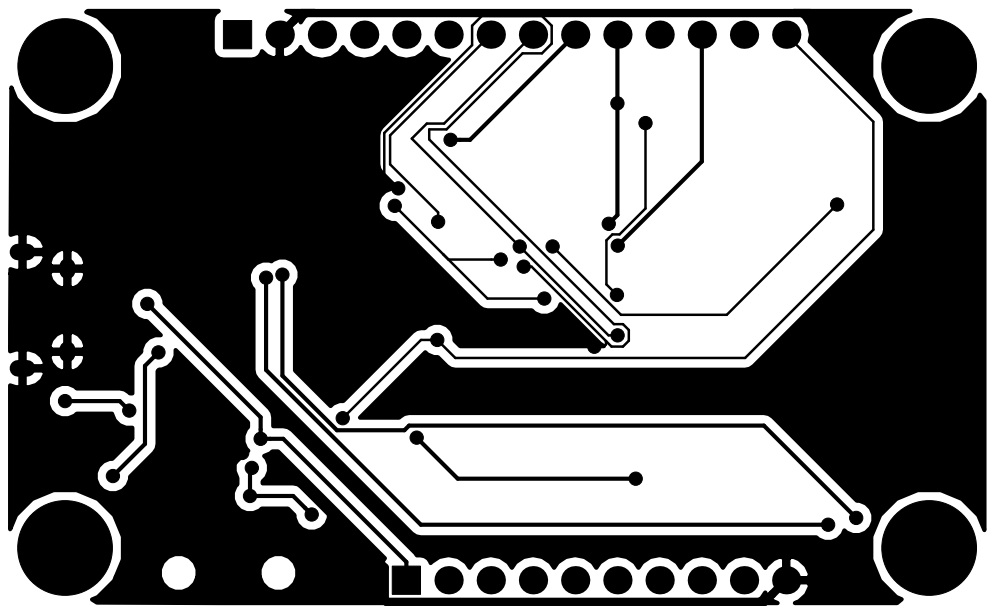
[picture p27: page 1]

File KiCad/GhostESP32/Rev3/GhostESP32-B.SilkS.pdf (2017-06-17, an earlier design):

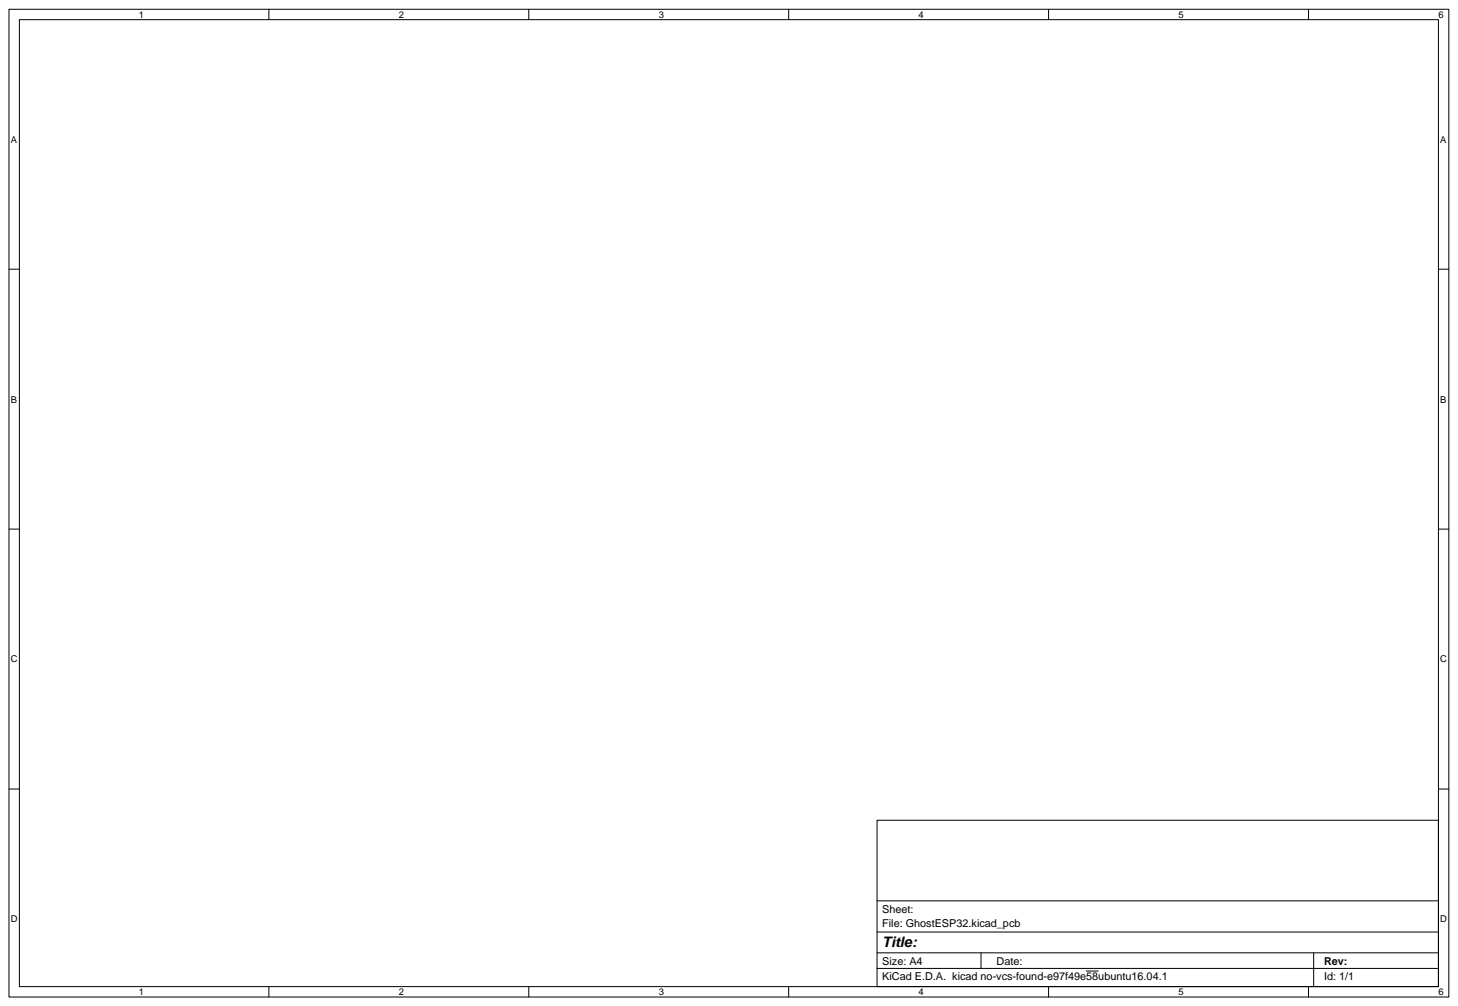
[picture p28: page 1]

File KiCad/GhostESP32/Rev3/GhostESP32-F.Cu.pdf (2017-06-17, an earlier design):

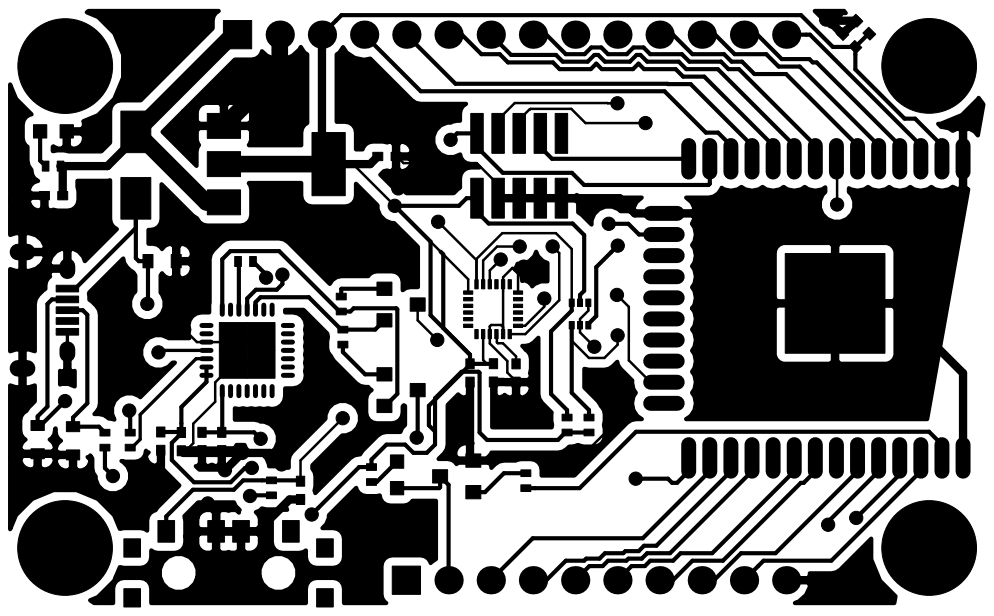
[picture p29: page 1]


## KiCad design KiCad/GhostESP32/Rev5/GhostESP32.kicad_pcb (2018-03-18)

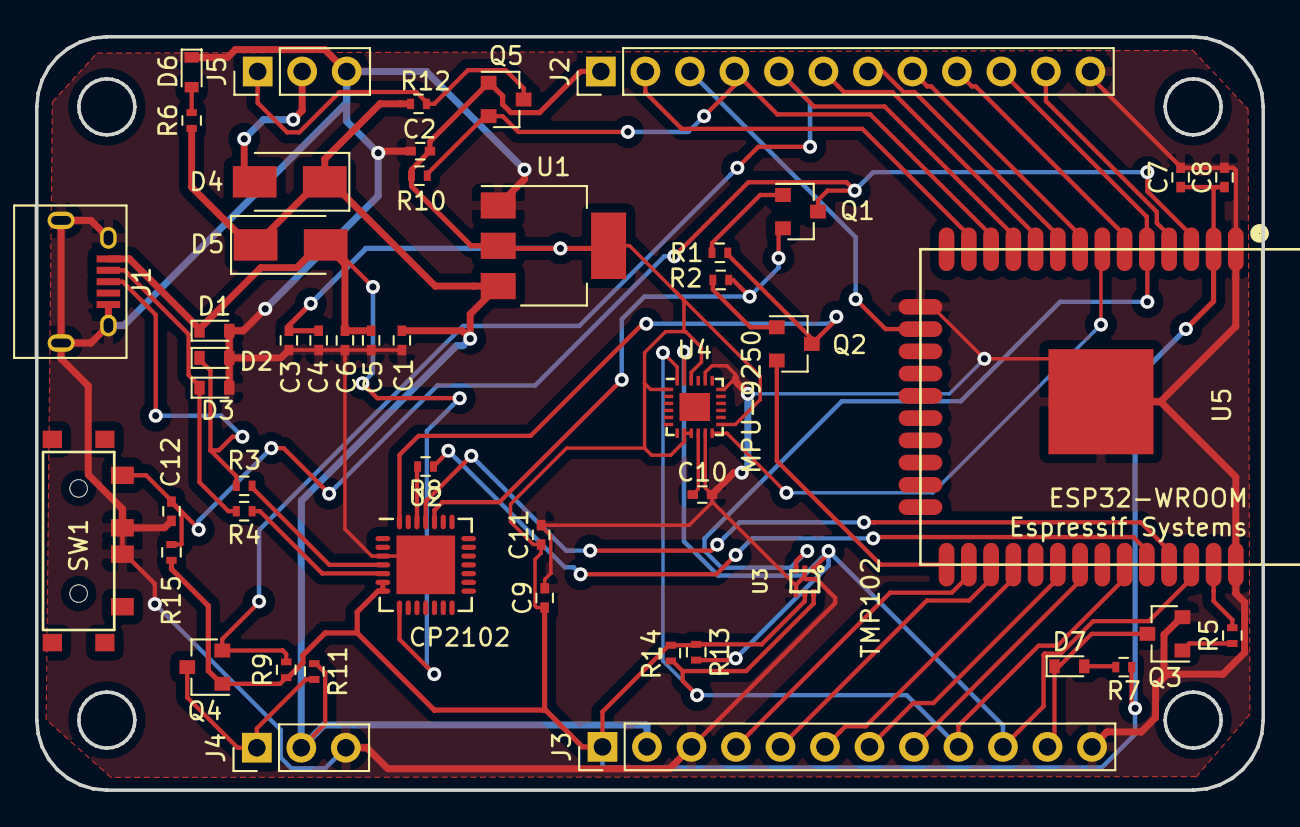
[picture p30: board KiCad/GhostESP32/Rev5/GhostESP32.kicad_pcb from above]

Board: 2 copper layers, 70.0 x 43.0 mm, 50 parts (0 on the bottom side), 44 nets.

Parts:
C1, C2, C3, C5: 10uF; C_0402
C4, C6, C9, C10: 100nF; C_0402
C7: 100uF; C_0402
C8, C12: 1uF; C_0402
C11: 10nF; C_0402
D1, D2, D3: ESD; D_0603
D4, D5: Schottky; D_SMA
D6: GREEN; D_0603
D7: YELLOW; D_0603
J1: USB_OTG; USB_Micro-B
J2, J3: CONN_01X12; Pin_Header_Straight_1x12_Pitch2.54mm
J4: STEERING; Pin_Header_Straight_1x03_Pitch2.54mm
J5: MOTOR; Pin_Header_Straight_1x03_Pitch2.54mm
Q1, Q2, Q3: Q_NPN_BEC; SOT-23
Q4, Q5: BSS138; SOT-23
R1, R2, R15: 12k; R_0402
R3, R4: 68; R_0402
R5, R9, R10, R11, R12, R13, R14: 10k; R_0402
R6: 1k; R_0402
R7: 330; R_0402
R8: 470; R_0402
SW1: SW_SPDT; SlideSwitchSpringReturn
U1: NCP1117-3.3_SOT223; SOT-223-3Lead_TabPin2
U2: CP2102; QFN-28-1EP_5x5mm_Pitch0.5mm
U3: TMP102; SOT563
U4: MPU-9250; QFN-24-1EP_3x3mm_Pitch0.4mm
U5: ESP-WROOM-32; ESP32-WROOM

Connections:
+3V3: C2.1, C3.1, C4.1, C7.1, C8.1, C9.1, C11.1, J2.1, J3.1, Q4.1, Q5.1, R7.1, R9.1, R10.1, R13.1, R14.1, R15.1, U1.2, U2.6, U2.7, U3.5, U4.1, U4.8, U4.9, U4.13, U4.22, U5.2
+5V: C1.1, D4.1, D5.1, J3.2, J4.2, R6.1, R11.1, R12.1, U1.3
+5V_ESC: D4.2, J5.2
DTR: Q2.3, R1.2, U2.28
EN: C12.1, Q1.3, R15.2, SW1.3, U5.3
GND: C1.2, C2.2, C3.2, C4.2, C5.2, C6.2, C7.2, C8.2, C9.2, C10.2, C11.2, C12.2, D1.2, D2.2, D3.2, D6.1, J1.5, J1.6, J2.12, J3.3, J3.12, J4.3, J5.3, Q3.2, SW1.2, U1.1, U2.3, U2.29, U3.2, U3.4, U4.11, U4.18, U4.20, U5.1, U5.15, U5.38, U5.39
I34: J2.9, U5.6
I35: U4.12, U5.7
I36: J2.11, U5.4
I39: J2.10, U3.3, U5.5
IO0: Q2.2, U5.25
IO4: J3.4, U5.26
IO13: J2.3, U5.16
IO14: J2.2, U5.13
IO16: J3.5, U5.27
IO17: J3.6, U5.28
IO18: J3.7, U5.30
IO19: J3.8, U5.31
IO21(SDA): J3.9, R14.2, U3.6, U4.24, U5.33
IO22(SCL): J3.10, R13.2, U3.1, U4.23, U5.36
IO23: R5.2, U5.37
IO25: J2.6, U5.10
IO26: J2.5, Q4.2, R9.2, U5.11
IO27: J2.4, Q5.2, R10.2, U5.12
IO32: J2.8, U5.8
IO33: J2.7, U5.9
LED: D7.1, J3.11, Q3.3
MOTOR_5V_PWM: J5.1, Q5.3, R12.2
unnamed: C10.1, U4.10
unnamed: D2.1, J1.3, R3.2
unnamed: D3.1, J1.2, R4.2
unnamed: D6.2, R6.2
unnamed: D7.2, R7.2
unnamed: Q1.1, R1.1
unnamed: Q2.1, R2.1
unnamed: Q3.1, R5.1
unnamed: R3.1, U2.4
unnamed: R4.1, U2.5
unnamed: R8.2, U2.26
RTS: Q1.2, R2.2, U2.24
RXD: U2.25, U5.35
STEERING_5V_PWM: J4.1, Q4.3, R11.2
TXD: R8.1, U5.34
VBUS: C5.1, C6.1, D1.1, D5.2, J1.1, U2.8

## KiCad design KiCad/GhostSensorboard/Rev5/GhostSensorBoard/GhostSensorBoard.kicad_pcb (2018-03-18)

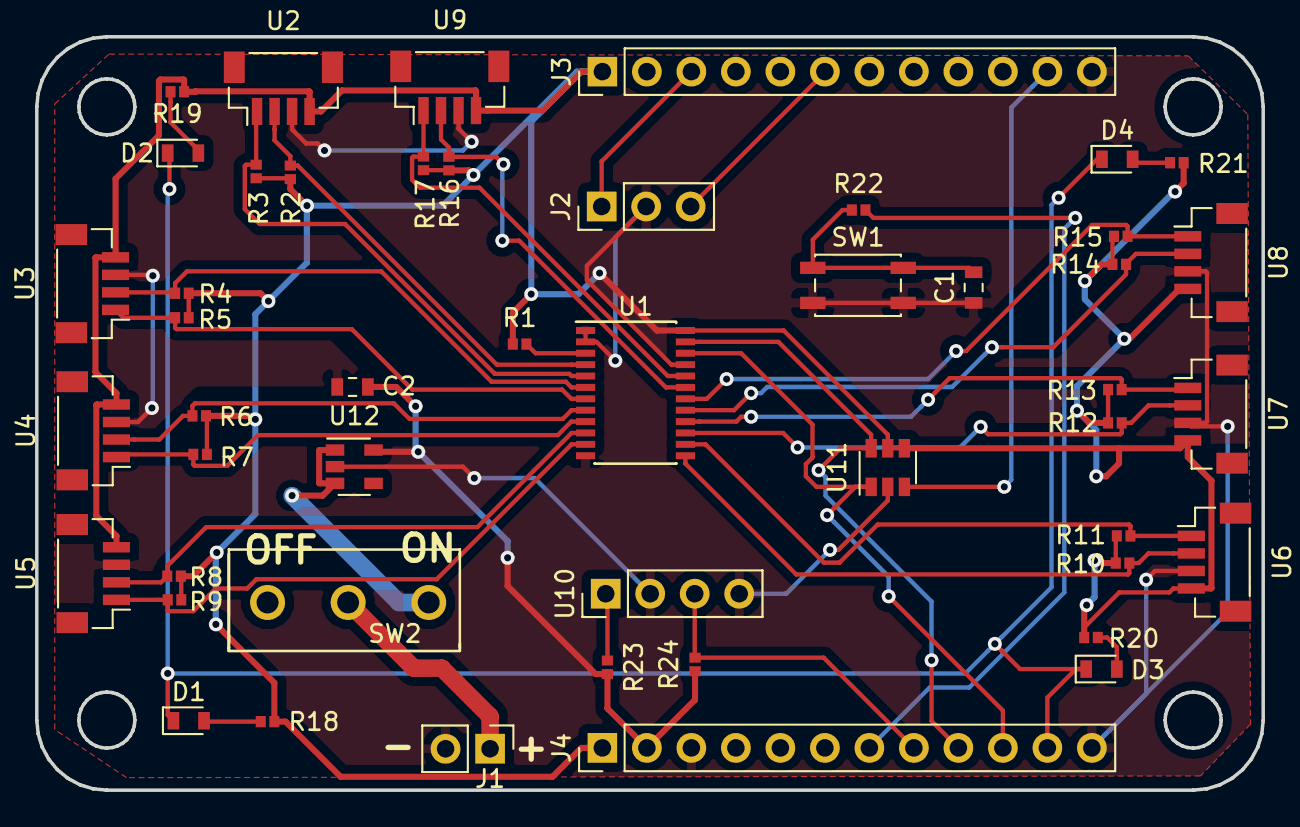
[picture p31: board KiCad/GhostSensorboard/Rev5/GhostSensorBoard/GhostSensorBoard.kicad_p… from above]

Board: 2 copper layers, 70.0 x 43.0 mm, 48 parts (0 on the bottom side), 36 nets.

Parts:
C1: 1nF; C_0603_1608Metric
C2: 2.2uF - 10uF; C_0603_1608Metric
D1, D2, D3, D4: LED; LED_0603_1608Metric
J1: Li-Po BATTERY; PinHeader_1x02_P2.54mm_Vertical
J2: Conn_01x03; PinHeader_1x03_P2.54mm_Vertical
J3, J4: Conn_01x12; PinHeader_1x12_P2.54mm_Vertical
R1: 2k2; R_0402_1005Metric
R2, R3, R4, R5, R6, R7, R8, R9, R10, R11, R12, R13, R14, R15, R16, R17: 1k; R_0402_1005Metric
R18, R19, R20, R21: 330; R_0402_1005Metric
R22: 470; R_0402_1005Metric
R23: 270; R_0402_1005Metric
R24: 10k; R_0402_1005Metric
SW1: SW_Push; SW_SPST_EVQP2
SW2: SW_SPDT; MFP106D
U1: TCA9548APWR; TSSOP-24_4.4x7.8mm_P0.65mm
U2, U3, U4, U5, U6, U7, U8, U9: GP2Y0E02B; JST_SH_BM04B-SRSS-TB_1x04_P1.00mm_Vertical
U10: Transmissive_Photo_Interrupter; PinHeader_1x04_P2.54mm_Vertical
U11: TMP102; SOT-23-6
U12: MIC5219-5.0; SOT-23-5

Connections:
+3V3: J3.1, J4.1, R1.1, R2.1, R3.1, R4.1, R5.1, R6.1, R7.1, R8.1, R9.1, R10.1, R11.1, R12.1, R13.1, R14.1, R15.1, R16.1, R17.1, R18.2, R19.2, R20.2, R21.2, U1.24, U2.4, U3.4, U4.4, U5.4, U6.4, U7.4, U8.4, U9.4, U11.4, U11.5
+5V: C2.1, J4.2, R23.2, R24.1, U12.5
+BATT: SW2.1, U12.1, U12.3
BUTTON: J4.7, R22.2
ENCODER: J4.8, R24.2, U10.3
GND: C1.1, C2.2, J1.2, J2.2, J3.12, J4.3, J4.12, SW1.2, U1.1, U1.2, U1.12, U1.21, U2.3, U3.3, U4.3, U5.3, U6.3, U7.3, U8.3, U9.3, U10.2, U10.4, U11.2, U12.2
I36: J3.11, U11.3
IO13: J2.1, J3.3
IO21(SDA): J4.9, U1.23, U11.6
IO22(SCL): J4.10, U1.22, U11.1
IO25: J2.3, J3.6
LED: D1.1, D2.1, D3.1, D4.1, J4.11
unnamed: C1.2, R22.1, SW1.1
unnamed: D1.2, R18.1
unnamed: D2.2, R19.1
unnamed: D3.2, R20.1
unnamed: D4.2, R21.1
unnamed: J1.1, SW2.2
unnamed: R1.2, U1.3
unnamed: R23.1, U10.1
SC0: R3.2, U1.5, U2.1
SC1: R5.2, U1.7, U3.1
SC2: R7.2, U1.9, U4.1
SC3: R9.2, U1.11, U5.1
SC4: R11.2, U1.14, U6.1
SC5: R13.2, U1.16, U7.1
SC6: R15.2, U1.18, U8.1
SC7: R17.2, U1.20, U9.1
SD0: R2.2, U1.4, U2.2
SD1: R4.2, U1.6, U3.2
SD2: R6.2, U1.8, U4.2
SD3: R8.2, U1.10, U5.2
SD4: R10.2, U1.13, U6.2
SD5: R12.2, U1.15, U7.2
SD6: R14.2, U1.17, U8.2
SD7: R16.2, U1.19, U9.2

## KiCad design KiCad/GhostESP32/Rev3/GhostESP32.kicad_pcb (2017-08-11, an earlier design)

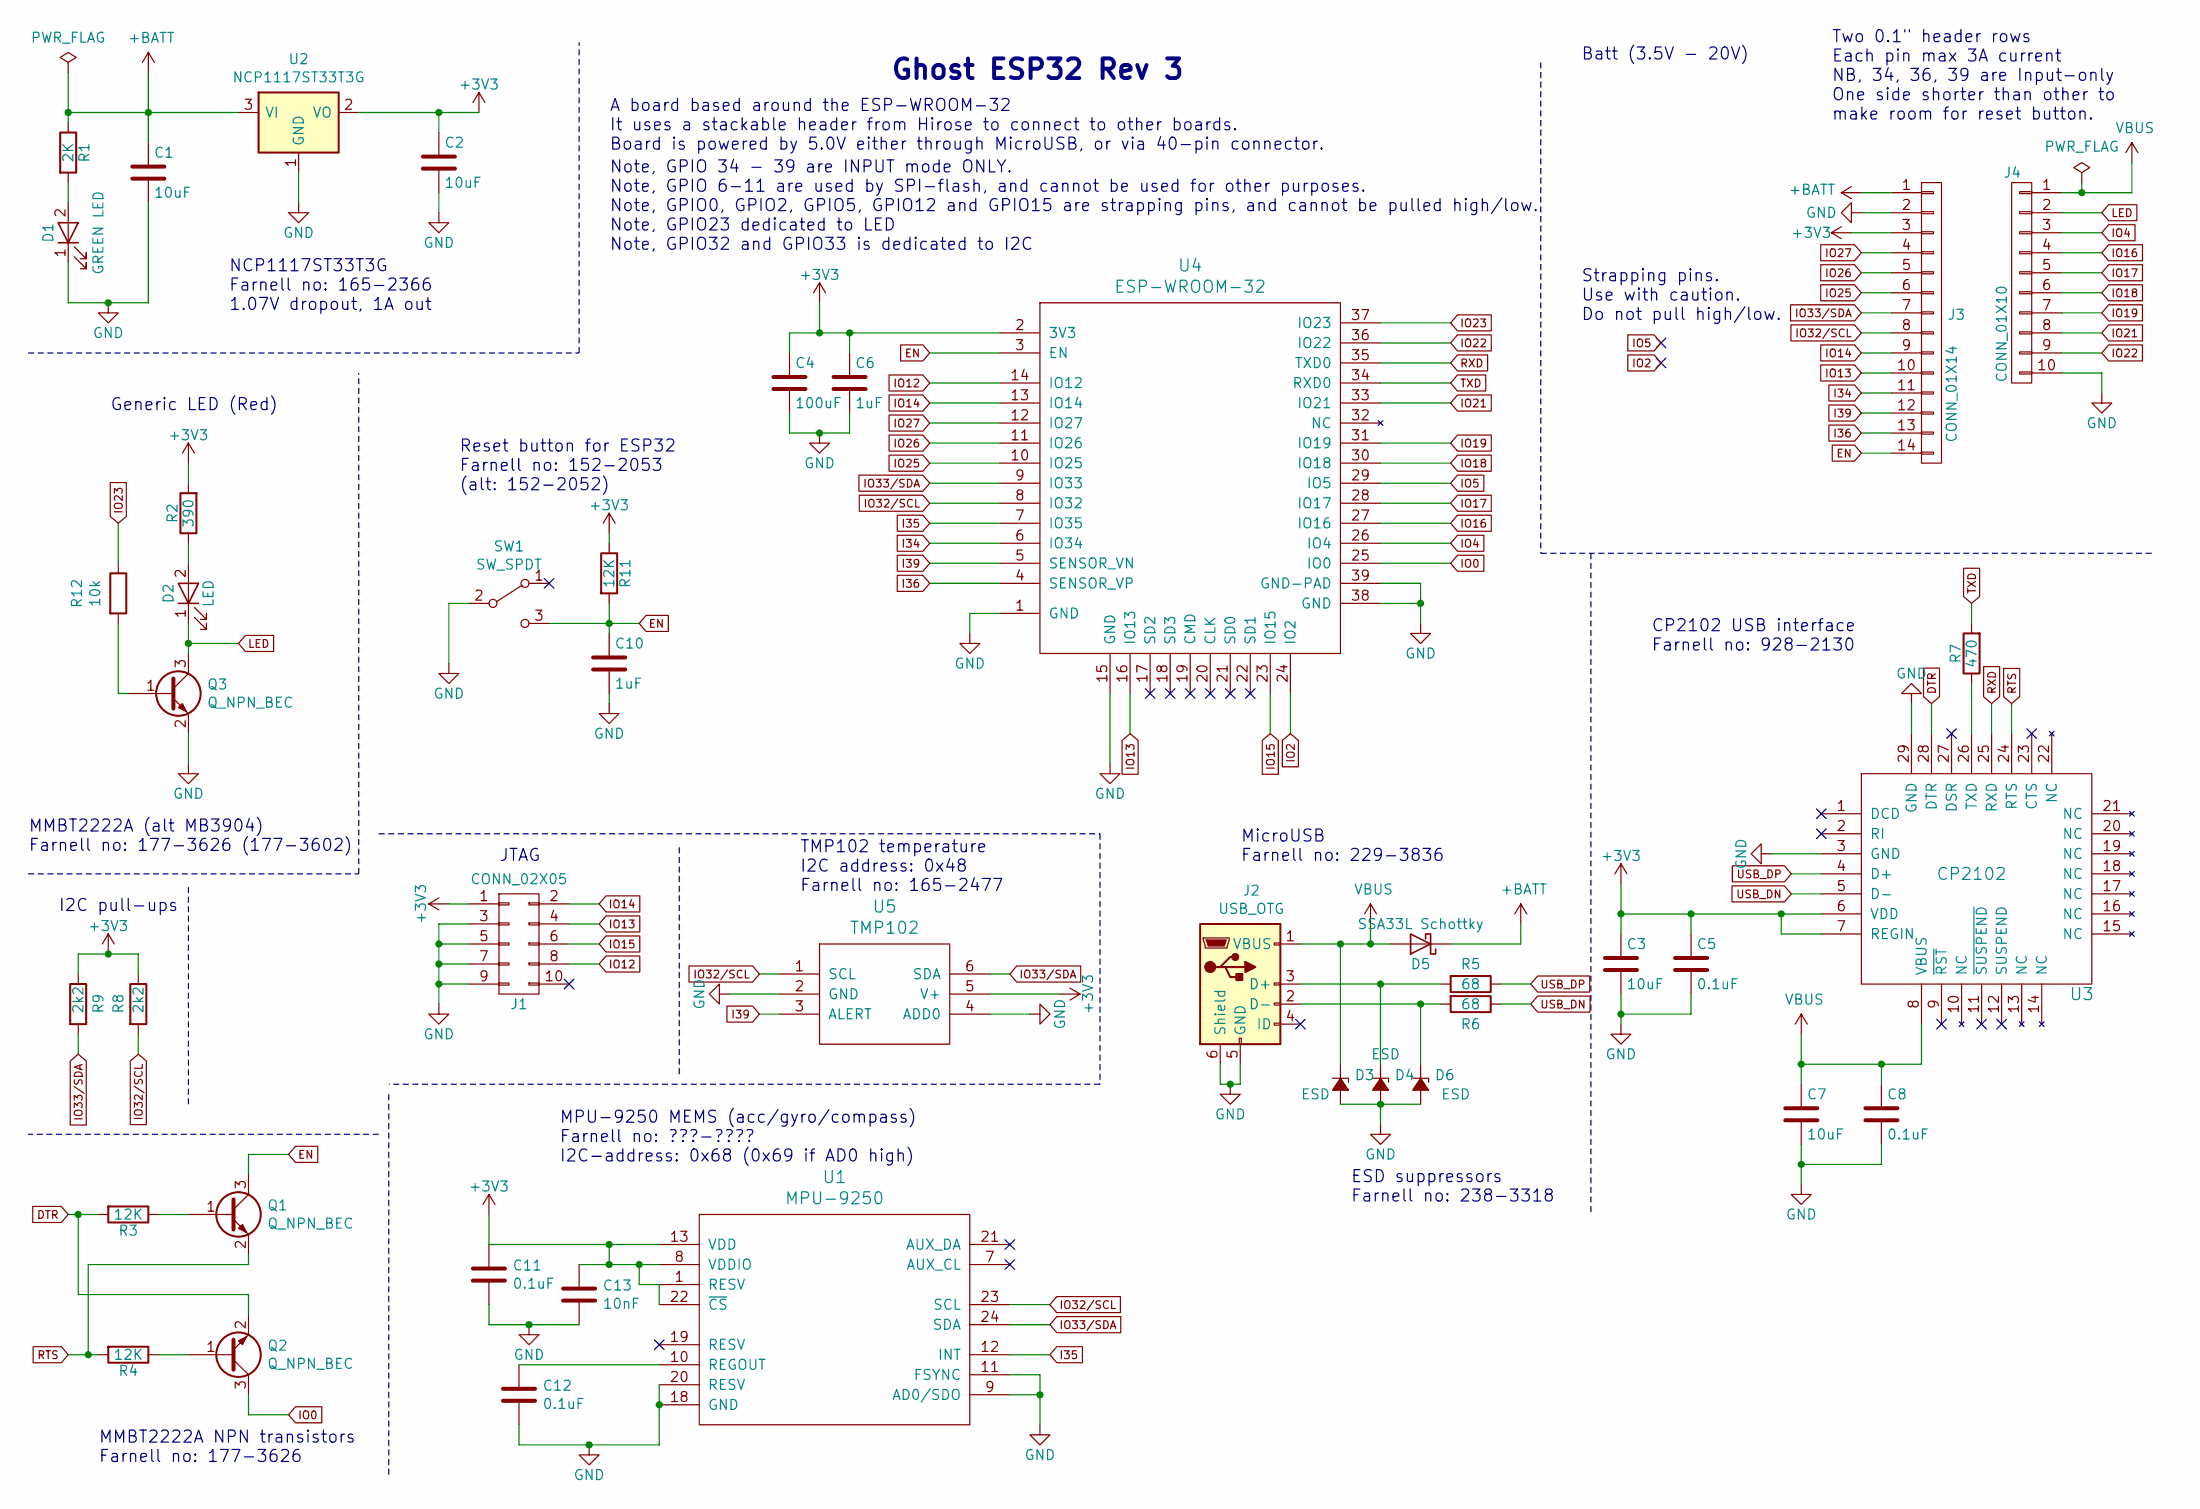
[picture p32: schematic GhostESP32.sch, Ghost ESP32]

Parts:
C1, C2, C3, C7: 10uF; C_0402
C4: 100uF; C_0402
C5, C8, C11, C12: 0.1uF; C_0402
C6, C10: 1uF; C_0402
C13: 10nF; C_0402
D1: GREEN LED; LED_0603
D2: LED; LED_0603
D3, D4, D6: ESD; D_0603
D5: SSA33L Schottky; D_SMA
J1: CONN_02X05; Pin_Header_Straight_2x05_Pitch1.27mm_SMD
J2: USB_OTG; USB_Micro-B
J3: CONN_01X14; Pin_Header_Straight_1x14_Pitch2.54mm
J4: CONN_01X10; Pin_Header_Straight_1x10_Pitch2.54mm
Q1, Q2, Q3: Q_NPN_BEC; SOT-23
R1: 2K; R_0402
R2: 390; R_0402
R3, R4, R11: 12K; R_0402
R5, R6: 68; R_0402
R7: 470; R_0402
R8, R9: 2k2; R_0402
R12: 10k; R_0402
SW1: SW_SPDT; SlideSwitchSpringReturn
U1: MPU-9250; QFN-24_3x3mm_Pitch0.4mm
U2: NCP1117ST33T3G; SOT-223-3Lead_TabPin2
U3: CP2102; QFN-28-1EP_5x5mm_Pitch0.5mm
U4: ESP-WROOM-32; ESP32-WROOM
U5: TMP102; SOT563

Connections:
+3V3: C2.1, C3.1, C4.1, C5.1, C6.1, C11.1, C13.1, J1.1, J3.3, R2.2, R8.1, R9.1, R11.1, U1.1 (RESV), U1.8 (VDDIO), U1.13 (VDD), U1.22 (~CS), U2.2 (VO), U3.6 (VDD), U3.7 (REGIN), U4.2 (3V3), U5.5 (V+)
+BATT: C1.1, D5.1 (K), J3.1, R1.1, U2.3 (VI)
DTR: Q2.2 (E), R3.2, U3.28 (DTR)
EN: C10.1, J3.14, Q1.3 (C), R11.2, SW1.3 (C), U4.3 (EN)
GND: C1.2, C2.2, C3.2, C4.2, C5.2, C6.2, C7.2, C8.2, C10.2, C11.2, C12.2, C13.2, D1.1 (K), D3.2 (A), D4.2 (A), D6.2 (A), J1.3, J1.5, J1.7, J1.9, J2.5 (GND), J2.6 (Shield), J3.2, J4.10, Q3.2 (E), SW1.2 (B), U1.9 (AD0/SDO), U1.11 (FSYNC), U1.18 (GND), U1.20 (RESV), U2.1 (GND), U3.3 (GND), U3.29 (GND), U4.1 (GND), U4.15 (GND), U4.38 (GND), U4.39 (GND-PAD), U5.2 (GND), U5.4 (ADD0)
I34: J3.11, U4.6 (IO34)
I35: U1.12 (INT), U4.7 (IO35)
I36: J3.13, U4.4 (SENSOR_VP)
I39: J3.12, U4.5 (SENSOR_VN), U5.3 (ALERT)
IO0: Q2.3 (C), U4.25 (IO0)
IO4: J4.3, U4.26 (IO4)
IO12: J1.8, U4.14 (IO12)
IO13: J1.4, J3.10, U4.16 (IO13)
IO14: J1.2, J3.9, U4.13 (IO14)
IO15: J1.6, U4.23 (IO15)
IO16: J4.4, U4.27 (IO16)
IO17: J4.5, U4.28 (IO17)
IO18: J4.6, U4.30 (IO18)
IO19: J4.7, U4.31 (IO19)
IO21: J4.8, U4.33 (IO21)
IO22: J4.9, U4.36 (IO22)
IO23: R12.1, U4.37 (IO23)
IO25: J3.6, U4.10 (IO25)
IO26: J3.5, U4.11 (IO26)
IO27: J3.4, U4.12 (IO27)
IO32/SCL: J3.8, R8.2, U1.23 (SCL), U4.8 (IO32), U5.1 (SCL)
IO33/SDA: J3.7, R9.2, U1.24 (SDA), U4.9 (IO33), U5.6 (SDA)
LED: D2.1 (K), J4.2, Q3.3 (C)
unnamed: C12.1, U1.10 (REGOUT)
unnamed: D1.2 (A), R1.2
unnamed: D2.2 (A), R2.1
unnamed: D4.1 (K), J2.3 (D+), R5.2
unnamed: D6.1 (K), J2.2 (D-), R6.2
unnamed: Q1.1 (B), R3.1
unnamed: Q2.1 (B), R4.1
unnamed: Q3.1 (B), R12.2
unnamed: R7.1, U3.26 (TXD)
RTS: Q1.2 (E), R4.2, U3.24 (RTS)
RXD: U3.25 (RXD), U4.35 (TXD0)
TXD: R7.2, U4.34 (RXD0)
USB_DN: R6.1, U3.5 (D-)
USB_DP: R5.1, U3.4 (D+)
VBUS: C7.1, C8.1, D3.1 (K), D5.2 (A), J2.1 (VBUS), J4.1, U3.8 (VBUS)

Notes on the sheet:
Ghost ESP32 Rev 3
A board based around the ESP-WROOM-32 It uses a stackable header from Hirose to connect to other boards. Board is powered by 5.0V either through MicroUSB, or via 40-pin connector.
MMBT2222A NPN transistors Farnell no: 177-3626
Generic LED (Red)
MicroUSB Farnell no: 229-3836
NCP1117ST33T3G Farnell no: 165-2366 1.07V dropout, 1A out
Note, GPIO 34 - 39 are INPUT mode ONLY. Note, GPIO 6-11 are used by SPI-flash, and cannot be used for other purposes. Note, GPIO0, GPIO2, GPIO5, GPIO12 and GPIO15 are strapping pins, and cannot be pulled high/low. Note, GPIO23 dedicated to LED Note, GPIO32 and GPIO33 is dedicated to I2C
Reset button for ESP32 Farnell no: 152-2053 (alt: 152-2052)
Strapping pins. Use with caution. Do not pull high/low.
I2C pull-ups
MMBT2222A (alt MB3904) Farnell no: 177-3626 (177-3602)
MPU-9250 MEMS (acc/gyro/compass) Farnell no: ???-???? I2C-address: 0x68 (0x69 if AD0 high)
CP2102 USB interface Farnell no: 928-2130
Two 0.1" header rows Each pin max 3A current NB, 34, 36, 39 are Input-only One side shorter than other to make room for reset button.
JTAG
Batt (3.5V - 20V)
ESD suppressors Farnell no: 238-3318
TMP102 temperature I2C address: 0x48 Farnell no: 165-2477

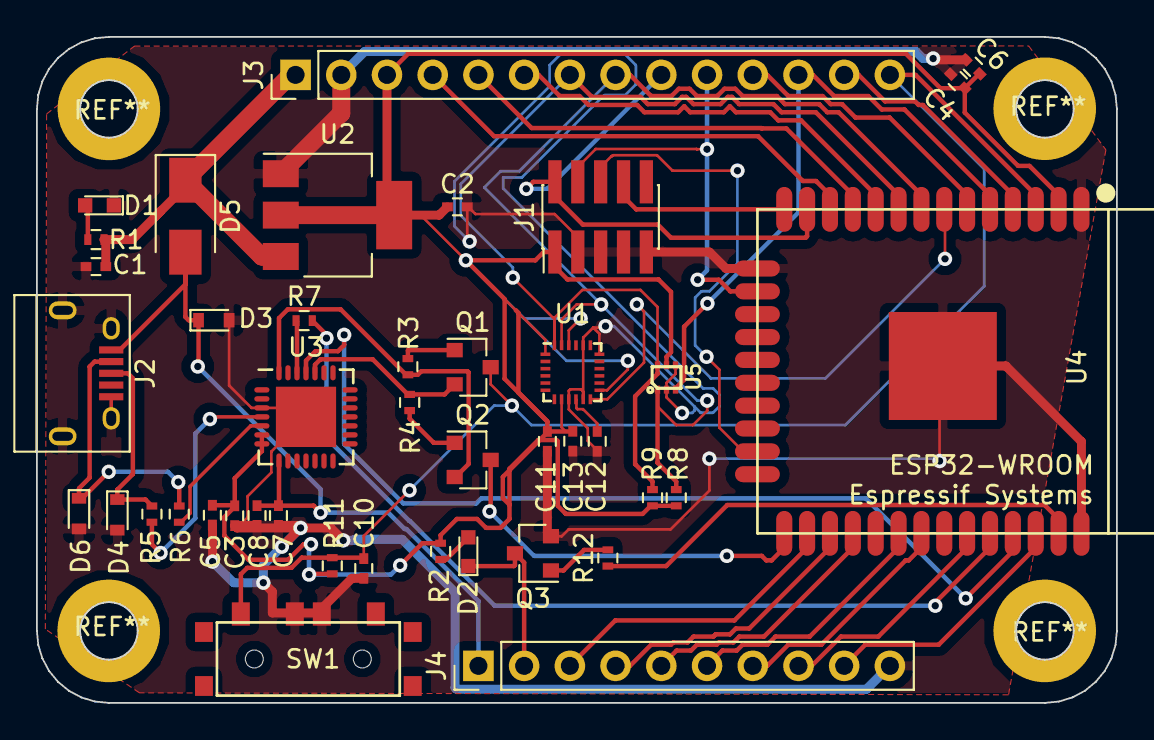
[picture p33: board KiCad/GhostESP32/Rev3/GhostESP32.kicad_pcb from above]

Board: 2 copper layers, 60.0 x 37.0 mm, 42 parts (0 on the bottom side), 43 nets.

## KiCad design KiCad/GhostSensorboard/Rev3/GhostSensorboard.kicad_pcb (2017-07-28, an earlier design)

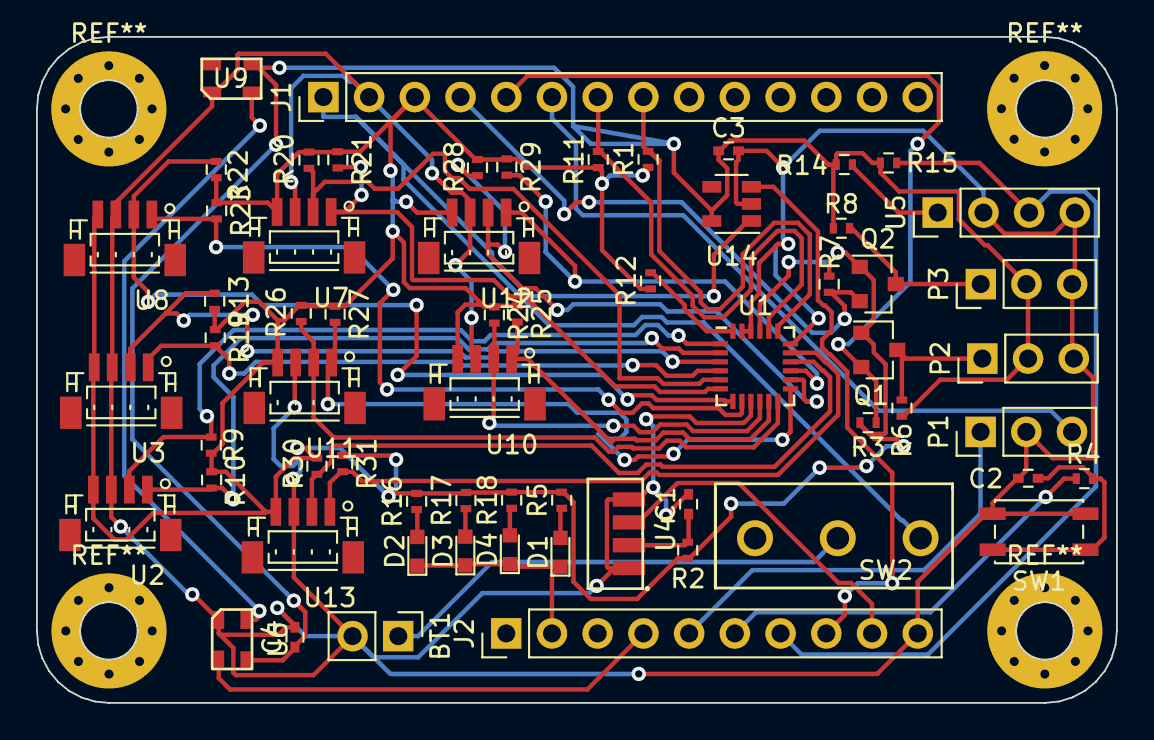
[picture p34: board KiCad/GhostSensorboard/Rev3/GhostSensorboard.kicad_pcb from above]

Board: 2 copper layers, 60.0 x 37.0 mm, 63 parts (0 on the bottom side), 44 nets.

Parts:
BT1: Battery_Cell; Pin_Header_Straight_1x02_Pitch2.54mm
C1: 1uF; C_0402
C2: 1nF; C_0402
C3: 2.2uF-10uF; C_0402
C4: 0.1uF; C_0402
D1, D2, D3, D4: LED; LED_0603
J1: CONN_01X14; Pin_Header_Straight_1x14_Pitch2.54mm
J2: CONN_01X10; Pin_Header_Straight_1x10_Pitch2.54mm
P1: StartModule; Pin_Header_Straight_1x03_Pitch2.54mm
P2: SteeringServo; Pin_Header_Straight_1x03_Pitch2.54mm
P3: Motor; Pin_Header_Straight_1x03_Pitch2.54mm
Q1, Q2: BSS138; SOT-23
R1, R11, R12: 2k2; R_0402
R2: 33-1k ohm; R_0402
R3, R6, R7, R8, R15: 10k; R_0402
R4: 470; R_0402
R5, R16, R17, R18: 330; R_0402
R9, R10, R13, R19, R20, R21, R22, R23, R24, R25, R26, R27, R28, R29, R30, R31: 1k; R_0402
R14: 270; R_0402
SW1: SW_Push; SW_SPST_EVQP2
SW2: SW_SPDT; MFP106D
U1: TCA9548ARGER; QFN-24_4x4mm_Pitch0.5mm_NoMask
U2, U3, U7, U8, U10, U11, U12, U13: GP2Y0E02B; JST_SH_BM04B-SRSS-TB_04x1.00mm_Straight
U4: TSOP752-TSOP754; TSOP75x
U5: Transmissive_Photo_Interrupter; Pin_Header_Straight_1x04_Pitch2.54mm
U6, U9: NeoPixelNano
U14: MIC5219-5.0; SOT-23-5

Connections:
+3V3: J1.3, Q1.1, Q2.1, R1.1, R2.2, R3.1, R5.2, R7.1, R9.1, R10.1, R11.1, R12.1, R13.1, R16.2, R17.2, R18.2, R19.1, R20.1, R21.1, R22.1, R23.1, R24.1, R25.1, R26.1, R27.1, R28.1, R29.1, R30.1, R31.1, U1.21, U2.4, U3.4, U7.4, U8.4, U10.4, U11.4, U12.4, U13.4
+5V: C3.1, C4.1, P2.2, P3.2, R6.1, R8.1, R14.2, R15.1, U6.4, U9.4, U14.5
+BATT: J1.1, SW2.1, U14.1
BUTTON: J2.6, R4.2
ENABLE5V: J2.8, U14.3
ENCODER: J2.7, R15.2, U5.3
GND: BT1.2, C1.2, C2.1, C3.2, C4.2, J1.2, J2.10, P1.2, P2.3, P3.3, SW1.2, U1.9, U1.18, U1.22, U1.23, U2.3, U3.3, U4.1, U4.4, U5.2, U5.4, U6.2, U7.3, U8.3, U9.2, U10.3, U11.3, U12.3, U13.3, U14.2
IO16: J2.4, U6.3
IO17: J2.5, P1.1
IO22: J2.9, U4.3
IO25: J1.6, P1.3
IO26: J1.5, Q1.2, R3.2
IO27: J1.4, Q2.2, R7.2
IO32/SCL: J1.8, R1.2, U1.19
IO33/SDA: J1.7, R11.2, U1.20
LED: D1.1, D2.1, D3.1, D4.1, J2.2
MOTOR_5V_PWM: P3.1, Q2.3, R8.2
unnamed: BT1.1, SW2.2
unnamed: C1.1, R2.1, U4.2
unnamed: C2.2, R4.1, SW1.1
unnamed: D1.2, R5.1
unnamed: D2.2, R16.1
unnamed: D3.2, R17.1
unnamed: D4.2, R18.1
unnamed: R12.2, U1.24
unnamed: R14.1, U5.1
unnamed: U6.1, U9.3
SC0: R10.2, U1.2, U2.1
SC1: R19.2, U1.4, U3.1
SC2: R21.2, U1.6, U7.1
SC3: R23.2, U1.8, U8.1
SC4: R25.2, U1.11, U10.1
SC5: R27.2, U1.13, U11.1
SC6: R29.2, U1.15, U12.1
SC7: R31.2, U1.17, U13.1
SD0: R9.2, U1.1, U2.2
SD1: R13.2, U1.3, U3.2
SD2: R20.2, U1.5, U7.2
SD3: R22.2, U1.7, U8.2
SD4: R24.2, U1.10, U10.2
SD5: R26.2, U1.12, U11.2
SD6: R28.2, U1.14, U12.2
SD7: R30.2, U1.16, U13.2
STEERING_5V_PWM: P2.1, Q1.3, R6.2

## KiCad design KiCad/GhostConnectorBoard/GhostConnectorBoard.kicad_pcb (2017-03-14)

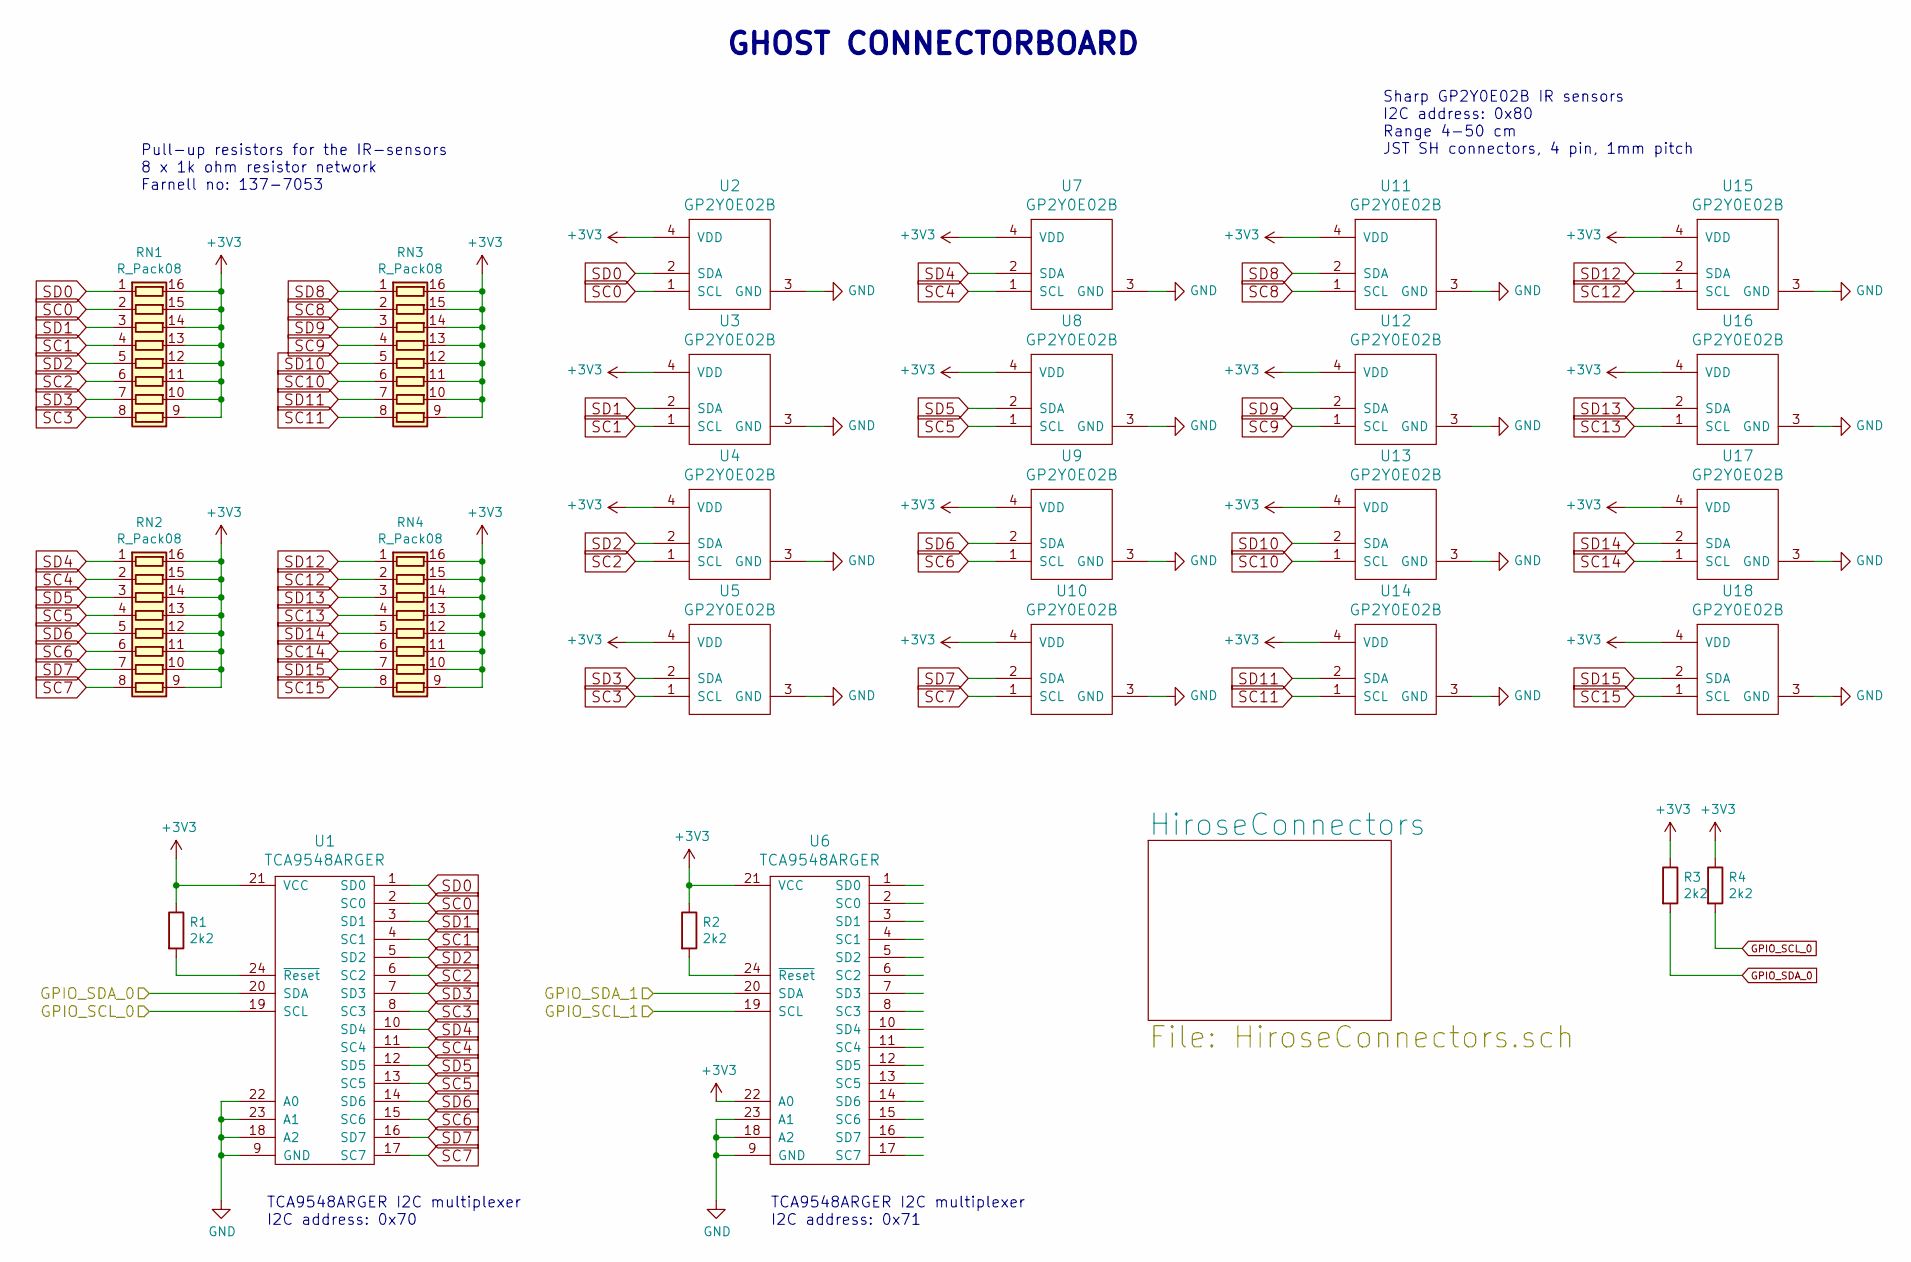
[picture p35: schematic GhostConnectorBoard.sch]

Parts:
R1, R2, R3, R4: 2k2; R_0603
RN1, RN2, RN3, RN4: R_Pack08; R_Array_Convex_8x0602
U1, U6: TCA9548ARGER; QFN-24_4x4mm_Pitch0.5mm
U2, U3, U4, U5, U7, U8, U9, U10, U11, U12, U13, U14, U15, U16, U17, U18: GP2Y0E02B; JST_SH_BM04B-SRSS-TB_04x1.00mm_Straight

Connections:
+3V3: R1.1, R2.1, R3.1, R4.1, RN1.9 (R8.2), RN1.10 (R7.2), RN1.11 (R6.2), RN1.12 (R5.2), RN1.13 (R4.2), RN1.14 (R3.2), RN1.15 (R2.2), RN1.16 (R1.2), RN2.9 (R8.2), RN2.10 (R7.2), RN2.11 (R6.2), RN2.12 (R5.2), RN2.13 (R4.2), RN2.14 (R3.2), RN2.15 (R2.2), RN2.16 (R1.2), RN3.9 (R8.2), RN3.10 (R7.2), RN3.11 (R6.2), RN3.12 (R5.2), RN3.13 (R4.2), RN3.14 (R3.2), RN3.15 (R2.2), RN3.16 (R1.2), RN4.9 (R8.2), RN4.10 (R7.2), RN4.11 (R6.2), RN4.12 (R5.2), RN4.13 (R4.2), RN4.14 (R3.2), RN4.15 (R2.2), RN4.16 (R1.2), U1.21 (VCC), U2.4 (VDD), U3.4 (VDD), U4.4 (VDD), U5.4 (VDD), U6.21 (VCC), U6.22 (A0), U7.4 (VDD), U8.4 (VDD), U9.4 (VDD), U10.4 (VDD), U11.4 (VDD), U12.4 (VDD), U13.4 (VDD), U14.4 (VDD), U15.4 (VDD), U16.4 (VDD), U17.4 (VDD), U18.4 (VDD)
/GPIO_SCL_1: U6.19 (SCL)
/GPIO_SDA_1: U6.20 (SDA)
GND: U1.9 (GND), U1.18 (A2), U1.22 (A0), U1.23 (A1), U2.3 (GND), U3.3 (GND), U4.3 (GND), U5.3 (GND), U6.9 (GND), U6.18 (A2), U6.23 (A1), U7.3 (GND), U8.3 (GND), U9.3 (GND), U10.3 (GND), U11.3 (GND), U12.3 (GND), U13.3 (GND), U14.3 (GND), U15.3 (GND), U16.3 (GND), U17.3 (GND), U18.3 (GND)
GPIO_SCL_0: R4.2, U1.19 (SCL)
GPIO_SDA_0: R3.2, U1.20 (SDA)
unnamed: R1.2, U1.24 (~Reset)
unnamed: R2.2, U6.24 (~Reset)
SC0: RN1.2 (R2.1), U1.2 (SC0), U2.1 (SCL)
SC1: RN1.4 (R4.1), U1.4 (SC1), U3.1 (SCL)
SC2: RN1.6 (R6.1), U1.6 (SC2), U4.1 (SCL)
SC3: RN1.8 (R8.1), U1.8 (SC3), U5.1 (SCL)
SC4: RN2.2 (R2.1), U1.11 (SC4), U7.1 (SCL)
SC5: RN2.4 (R4.1), U1.13 (SC5), U8.1 (SCL)
SC6: RN2.6 (R6.1), U1.15 (SC6), U9.1 (SCL)
SC7: RN2.8 (R8.1), U1.17 (SC7), U10.1 (SCL)
SC8: RN3.2 (R2.1), U11.1 (SCL)
SC9: RN3.4 (R4.1), U12.1 (SCL)
SC10: RN3.6 (R6.1), U13.1 (SCL)
SC11: RN3.8 (R8.1), U14.1 (SCL)
SC12: RN4.2 (R2.1), U15.1 (SCL)
SC13: RN4.4 (R4.1), U16.1 (SCL)
SC14: RN4.6 (R6.1), U17.1 (SCL)
SC15: RN4.8 (R8.1), U18.1 (SCL)
SD0: RN1.1 (R1.1), U1.1 (SD0), U2.2 (SDA)
SD1: RN1.3 (R3.1), U1.3 (SD1), U3.2 (SDA)
SD2: RN1.5 (R5.1), U1.5 (SD2), U4.2 (SDA)
SD3: RN1.7 (R7.1), U1.7 (SD3), U5.2 (SDA)
SD4: RN2.1 (R1.1), U1.10 (SD4), U7.2 (SDA)
SD5: RN2.3 (R3.1), U1.12 (SD5), U8.2 (SDA)
SD6: RN2.5 (R5.1), U1.14 (SD6), U9.2 (SDA)
SD7: RN2.7 (R7.1), U1.16 (SD7), U10.2 (SDA)
SD8: RN3.1 (R1.1), U11.2 (SDA)
SD9: RN3.3 (R3.1), U12.2 (SDA)
SD10: RN3.5 (R5.1), U13.2 (SDA)
SD11: RN3.7 (R7.1), U14.2 (SDA)
SD12: RN4.1 (R1.1), U15.2 (SDA)
SD13: RN4.3 (R3.1), U16.2 (SDA)
SD14: RN4.5 (R5.1), U17.2 (SDA)
SD15: RN4.7 (R7.1), U18.2 (SDA)

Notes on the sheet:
Sharp GP2Y0E02B IR sensors I2C address: 0x80 Range 4-50 cm JST SH connectors, 4 pin, 1mm pitch
Pull-up resistors for the IR-sensors 8 x 1k ohm resistor network Farnell no: 137-7053
TCA9548ARGER I2C multiplexer I2C address: 0x70
TCA9548ARGER I2C multiplexer I2C address: 0x71
GHOST CONNECTORBOARD

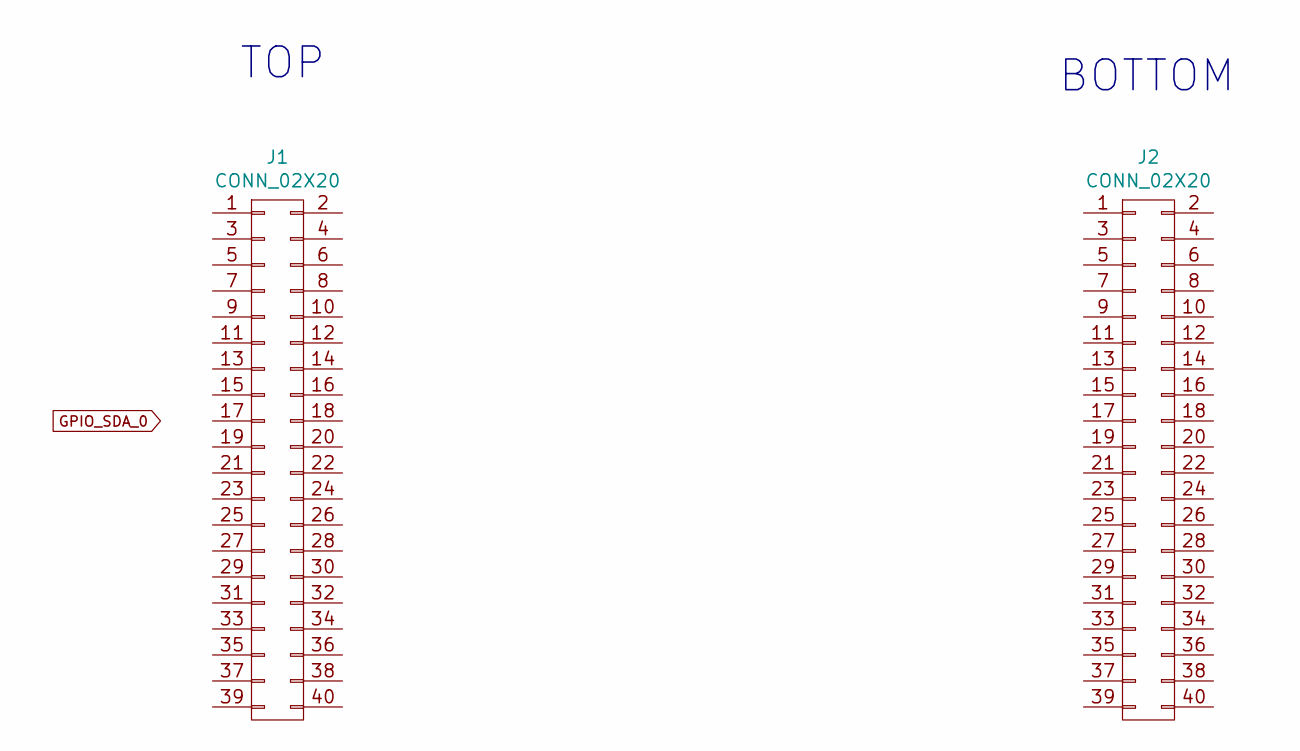
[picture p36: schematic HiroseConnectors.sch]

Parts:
J1, J2: CONN_02X20; hrs-fx8c-40p-sv

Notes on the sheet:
TOP
BOTTOM

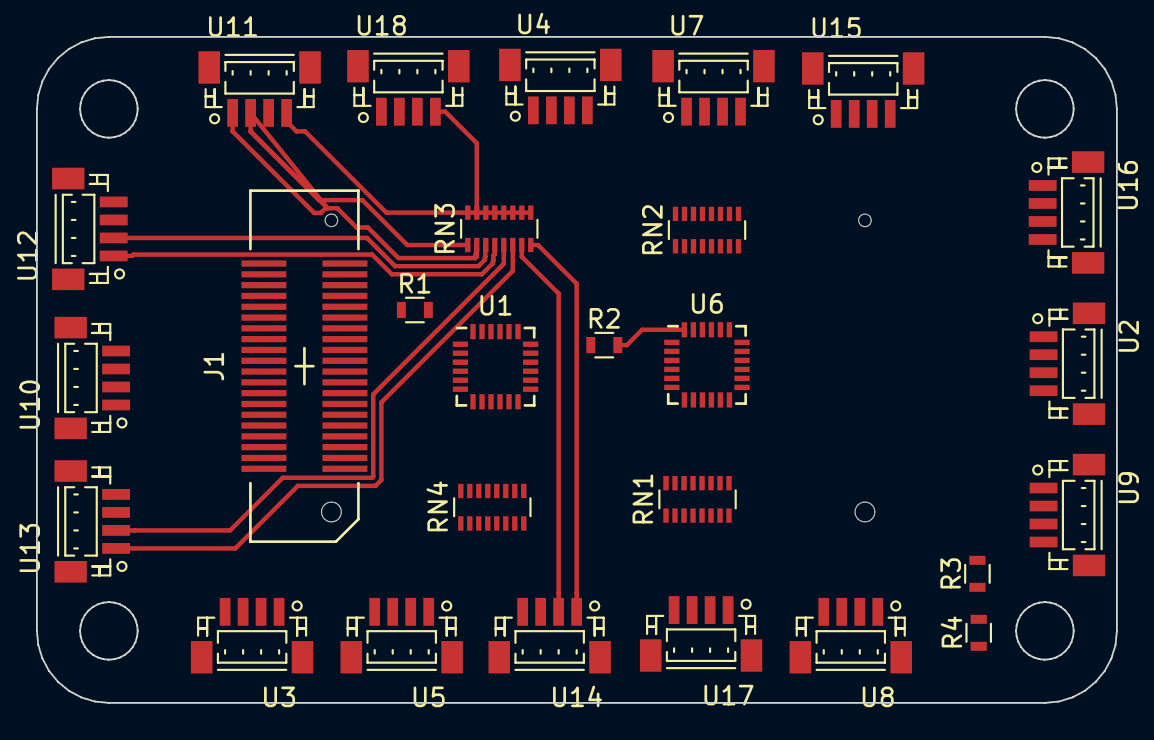
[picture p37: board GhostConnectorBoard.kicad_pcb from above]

Board: 2 copper layers, 60.0 x 37.0 mm, 28 parts (1 on the bottom side), 38 nets.

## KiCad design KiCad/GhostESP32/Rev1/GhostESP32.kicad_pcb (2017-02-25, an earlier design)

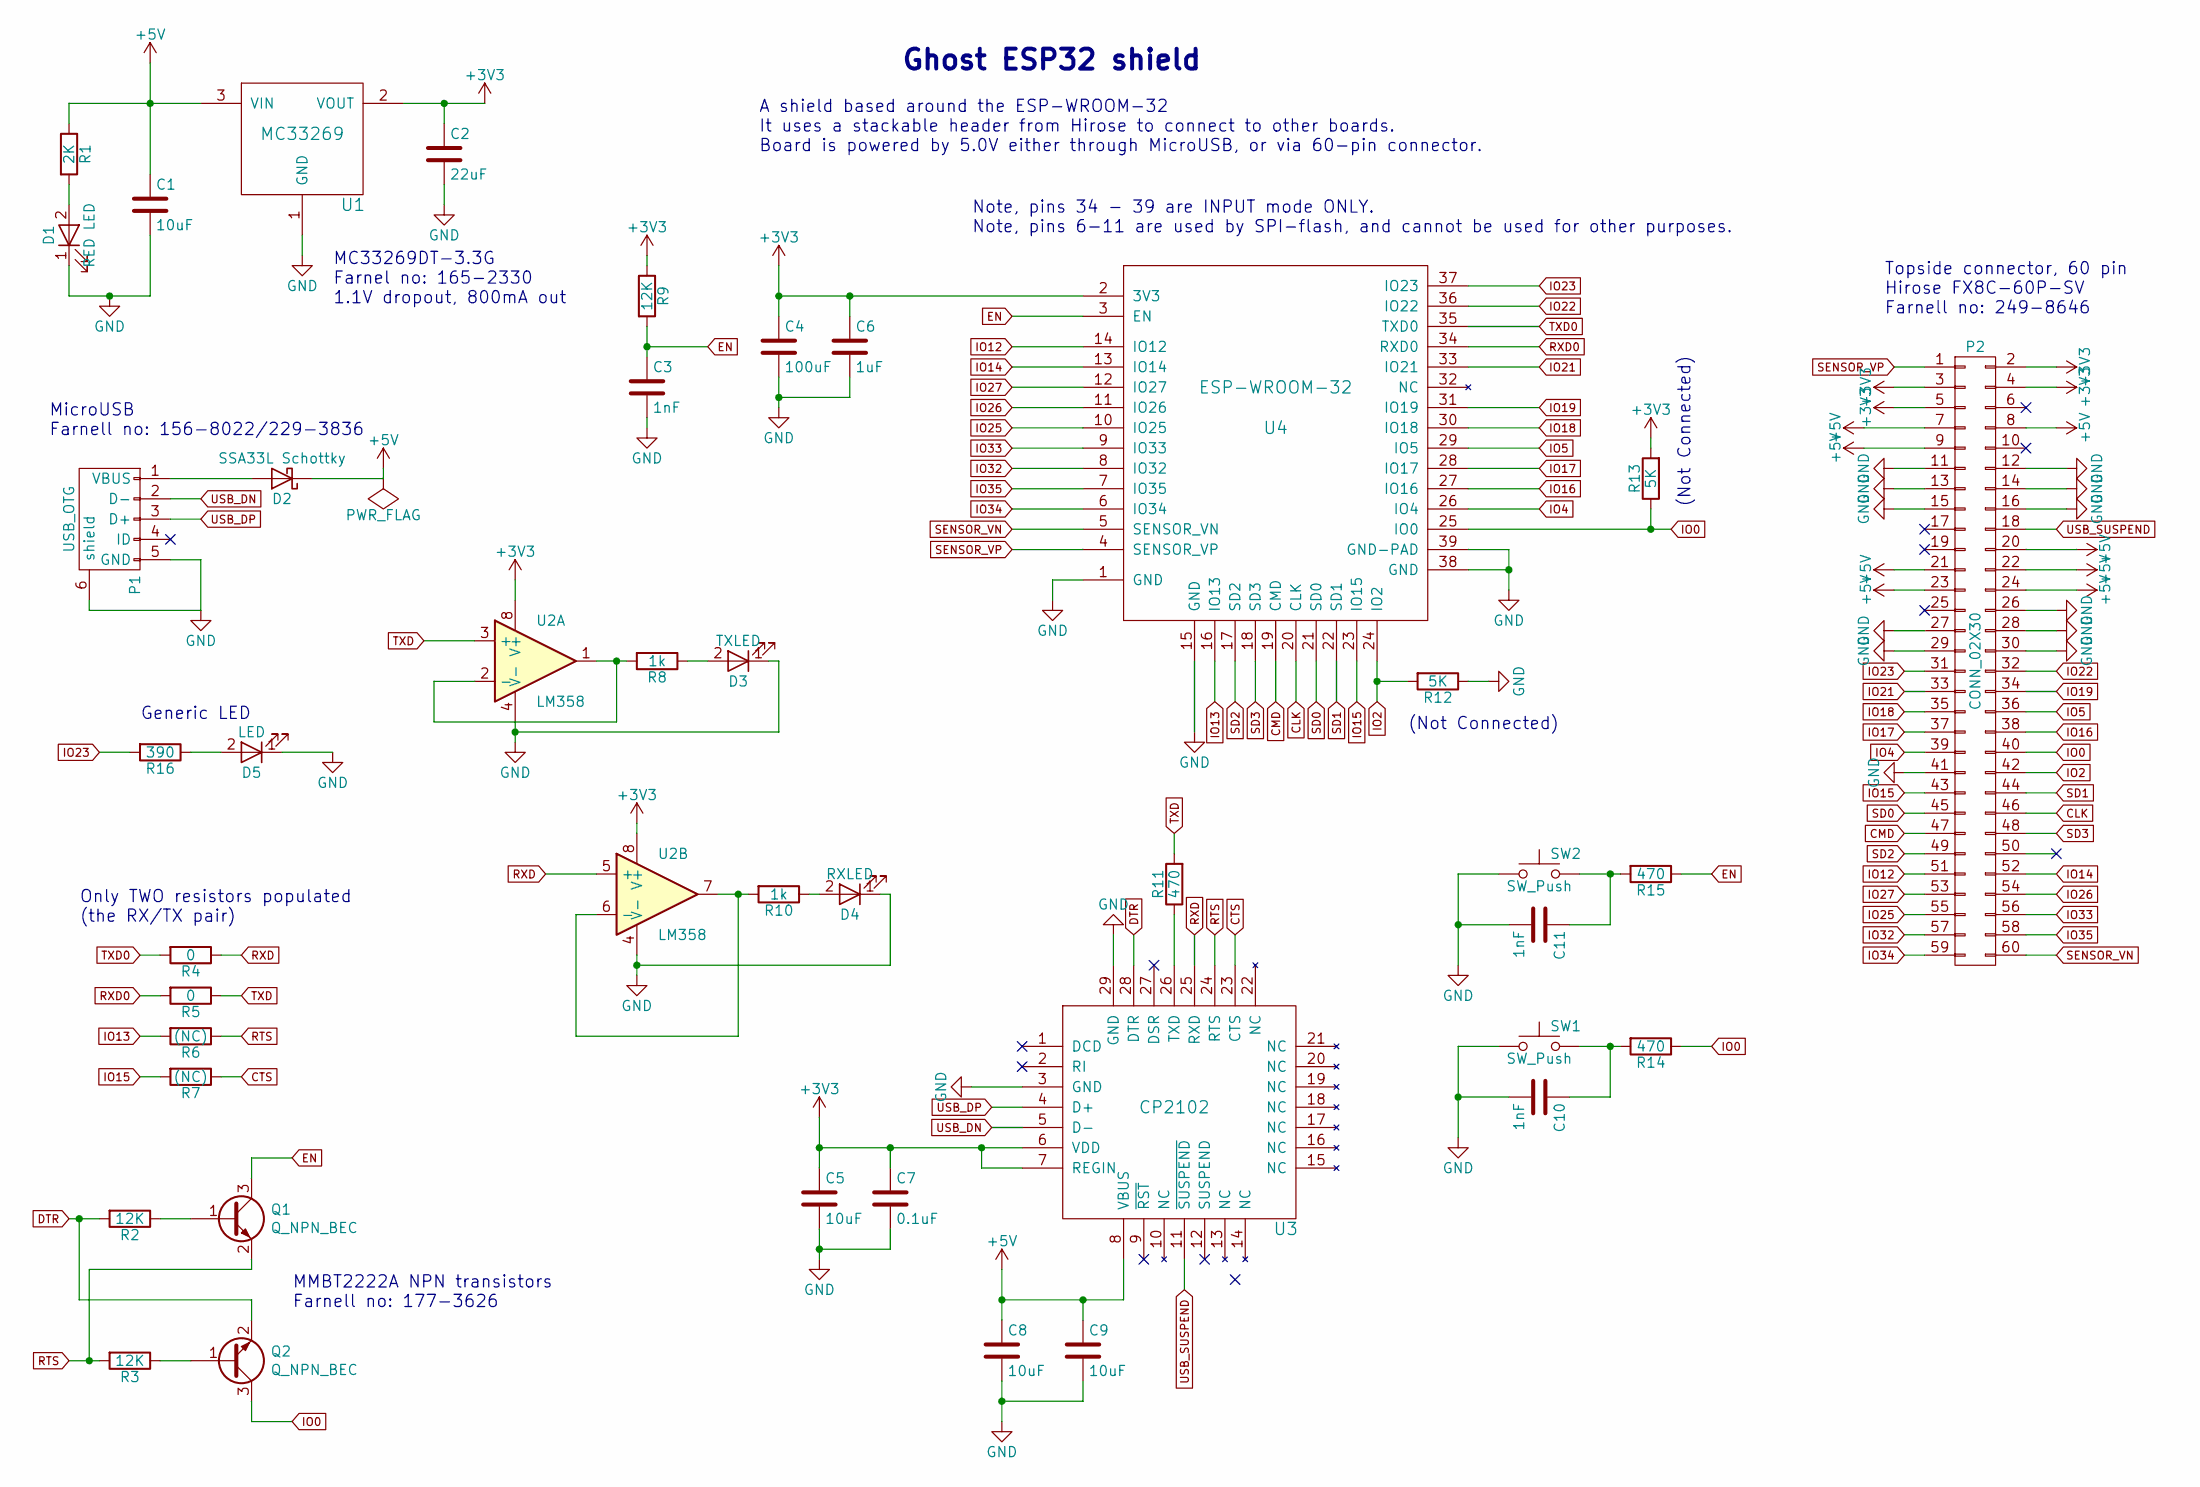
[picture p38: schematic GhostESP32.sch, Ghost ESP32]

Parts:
C1, C5, C8, C9: 10uF; C_0603
C2: 22uF; C_0603
C3, C10, C11: 1nF; C_0603
C4: 100uF; C_0603
C6: 1uF; C_0603
C7: 0.1uF; C_0603
D1: RED LED; LED_0603
D2: SSA33L Schottky; D_SMA_Standard
D3: TXLED; LED_0603
D4: RXLED; LED_0603
D5: LED; LED_0603
P1: USB_OTG; USB_Micro-B
P2: CONN_02X30; hrs-fx8c-60p-sv
Q1, Q2: Q_NPN_BEC
R1: 2K; R_0603
R2, R3, R9: 12K; R_0603
R4, R5: 0; R_0603
R6, R7: (NC); R_0603
R8, R10: 1k; R_0603
R11, R14, R15: 470; R_0603
R12, R13: 5K; R_0603
R16: 390; R_0603
SW1, SW2: SW_Push; SW_SPST_EVQP2
U1: MC33269; TO-252-2Lead
U2: LM358; SOIC-8_3.9x4.9mm_Pitch1.27mm
U3: CP2102; QFN-28-1EP_5x5mm_Pitch0.5mm
U4: ESP-WROOM-32; ESP32-WROOM

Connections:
+3V3: C2.1, C4.1, C5.1, C6.1, C7.1, P2.2, P2.3, P2.4, P2.5, R9.1, R13.2, U1.2 (VOUT), U2.8 (V+), U3.6 (VDD), U3.7 (REGIN), U4.2 (3V3)
+5V: C1.1, C8.1, C9.1, D2.1 (K), P2.7, P2.8, P2.9, P2.20, P2.21, P2.22, P2.23, P2.24, R1.1, U1.3 (VIN), U3.8 (VBUS)
CLK: P2.46, U4.20 (CLK)
CMD: P2.47, U4.19 (CMD)
CTS: R7.1, U3.23 (CTS)
DTR: Q2.2 (E), R2.2, U3.28 (DTR)
EN: C3.1, Q1.3 (C), R9.2, R15.1, U4.3 (EN)
GND: C1.2, C2.2, C3.2, C4.2, C5.2, C6.2, C7.2, C8.2, C9.2, C10.2, C11.2, D1.1 (K), D3.1 (K), D4.1 (K), D5.1 (K), P1.5 (GND), P1.6 (shield), P2.11, P2.12, P2.13, P2.14, P2.15, P2.16, P2.26, P2.27, P2.28, P2.29, P2.30, P2.41, R12.1, SW1.1, SW2.1, U1.1 (GND), U2.4 (V-), U3.3 (GND), U3.29 (GND), U4.1 (GND), U4.15 (GND), U4.38 (GND), U4.39 (GND-PAD); also elsewhere on the board
IO0: P2.40, Q2.3 (C), R13.1, R14.1, U4.25 (IO0)
IO2: P2.42, R12.2, U4.24 (IO2)
IO4: P2.39, U4.26 (IO4)
IO5: P2.36, U4.29 (IO5)
IO12: P2.51, U4.14 (IO12)
IO13: R6.2, U4.16 (IO13)
IO14: P2.52, U4.13 (IO14)
IO15: P2.43, R7.2, U4.23 (IO15)
IO16: P2.38, U4.27 (IO16)
IO17: P2.37, U4.28 (IO17)
IO18: P2.35, U4.30 (IO18)
IO19: P2.34, U4.31 (IO19)
IO21: P2.33, U4.33 (IO21)
IO22: P2.32, U4.36 (IO22)
IO23: P2.31, R16.2, U4.37 (IO23)
IO25: P2.55, U4.10 (IO25)
IO26: P2.54, U4.11 (IO26)
IO27: P2.53, U4.12 (IO27)
IO32: P2.57, U4.8 (IO32)
IO33: P2.56, U4.9 (IO33)
IO34: P2.59, U4.6 (IO34)
IO35: P2.58, U4.7 (IO35)
unnamed: C10.1, R14.2, SW1.2
unnamed: C11.1, R15.2, SW2.2
unnamed 32: D1.2 (A), R1.2; also elsewhere on the board
unnamed: D2.2 (A), P1.1 (VBUS)
unnamed 34: D3.2 (A), R8.1; also elsewhere on the board
unnamed 35: D4.2 (A), R10.1; also elsewhere on the board
unnamed: D5.2 (A), R16.1
unnamed: Q1.1 (B), R2.1
unnamed: Q2.1 (B), R3.1
unnamed: R8.2, U2.1, U2.2 (-)
unnamed: R10.2, U2.6 (-), U2.7
unnamed: R11.1, U3.26 (TXD)
RTS: Q1.2 (E), R3.2, R6.1, U3.24 (RTS)
RXD: R4.1, U2.5 (+), U3.25 (RXD)
RXD0: R5.2, U4.34 (RXD0)
SD0: P2.45, U4.21 (SD0)
SD1: P2.44, U4.22 (SD1)
SD2: P2.49, U4.17 (SD2)
SD3: P2.48, U4.18 (SD3)
SENSOR_VN: P2.60, U4.5 (SENSOR_VN)
SENSOR_VP: P2.1, U4.4 (SENSOR_VP)
TXD: R5.1, R11.2, U2.3 (+)
TXD0: R4.2, U4.35 (TXD0)
USB_DN: P1.2 (D-), U3.5 (D-)
USB_DP: P1.3 (D+), U3.4 (D+)
USB_SUSPEND: P2.18, U3.11 (~SUSPEND)

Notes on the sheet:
Ghost ESP32 shield
A shield based around the ESP-WROOM-32 It uses a stackable header from Hirose to connect to other boards. Board is powered by 5.0V either through MicroUSB, or via 60-pin connector.
Topside connector, 60 pin Hirose FX8C-60P-SV Farnell no: 249-8646
Only TWO resistors populated (the RX/TX pair)
(Not Connected)
MMBT2222A NPN transistors Farnell no: 177-3626
Generic LED
MicroUSB Farnell no: 156-8022/229-3836
MC33269DT-3.3G Farnel no: 165-2330 1.1V dropout, 800mA out
Note, pins 34 - 39 are INPUT mode ONLY. Note, pins 6-11 are used by SPI-flash, and cannot be used for other purposes.

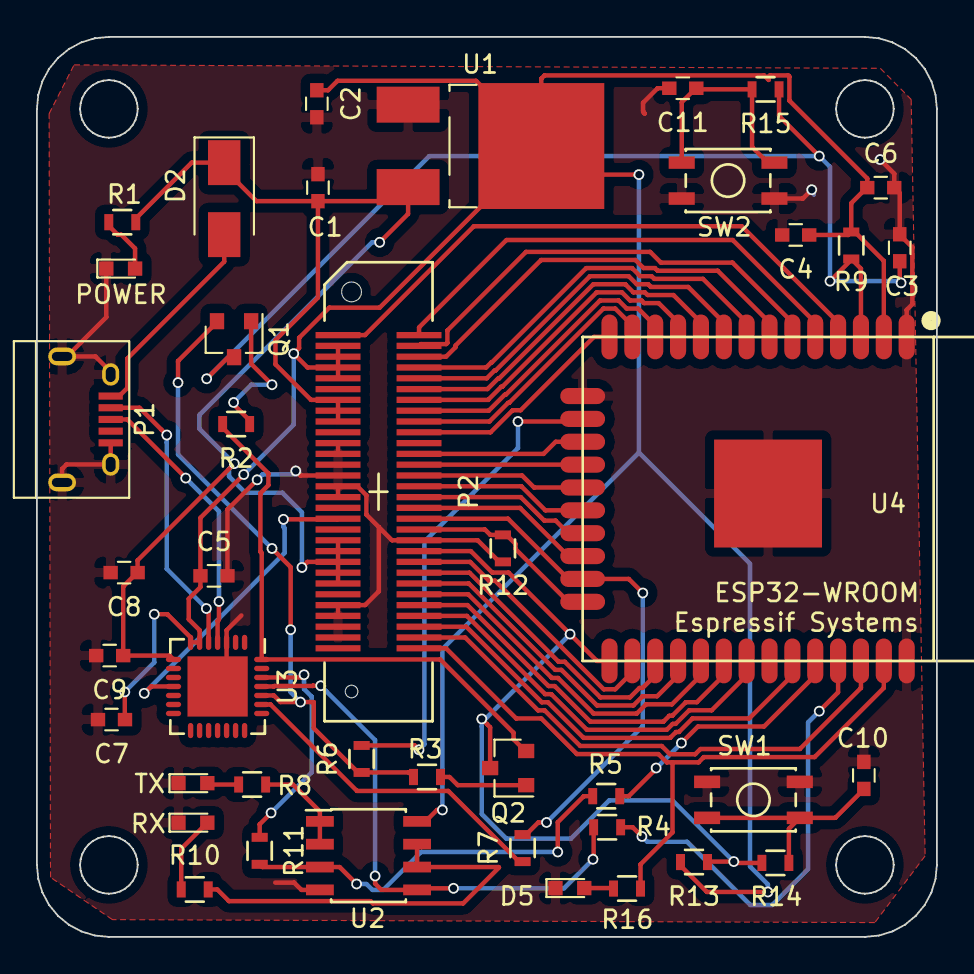
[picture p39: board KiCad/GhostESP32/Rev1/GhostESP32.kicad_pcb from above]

Board: 2 copper layers, 50.0 x 50.0 mm, 42 parts (0 on the bottom side), 56 nets.

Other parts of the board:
POWER: RED LED; LED_0603
RX: RXLED; LED_0603
TX: TXLED; LED_0603

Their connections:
GND: POWER.1, RX.1, TX.1; also elsewhere on the board
unnamed 32: POWER.2; also elsewhere on the board
unnamed 34: TX.2; also elsewhere on the board
unnamed 35: RX.2; also elsewhere on the board

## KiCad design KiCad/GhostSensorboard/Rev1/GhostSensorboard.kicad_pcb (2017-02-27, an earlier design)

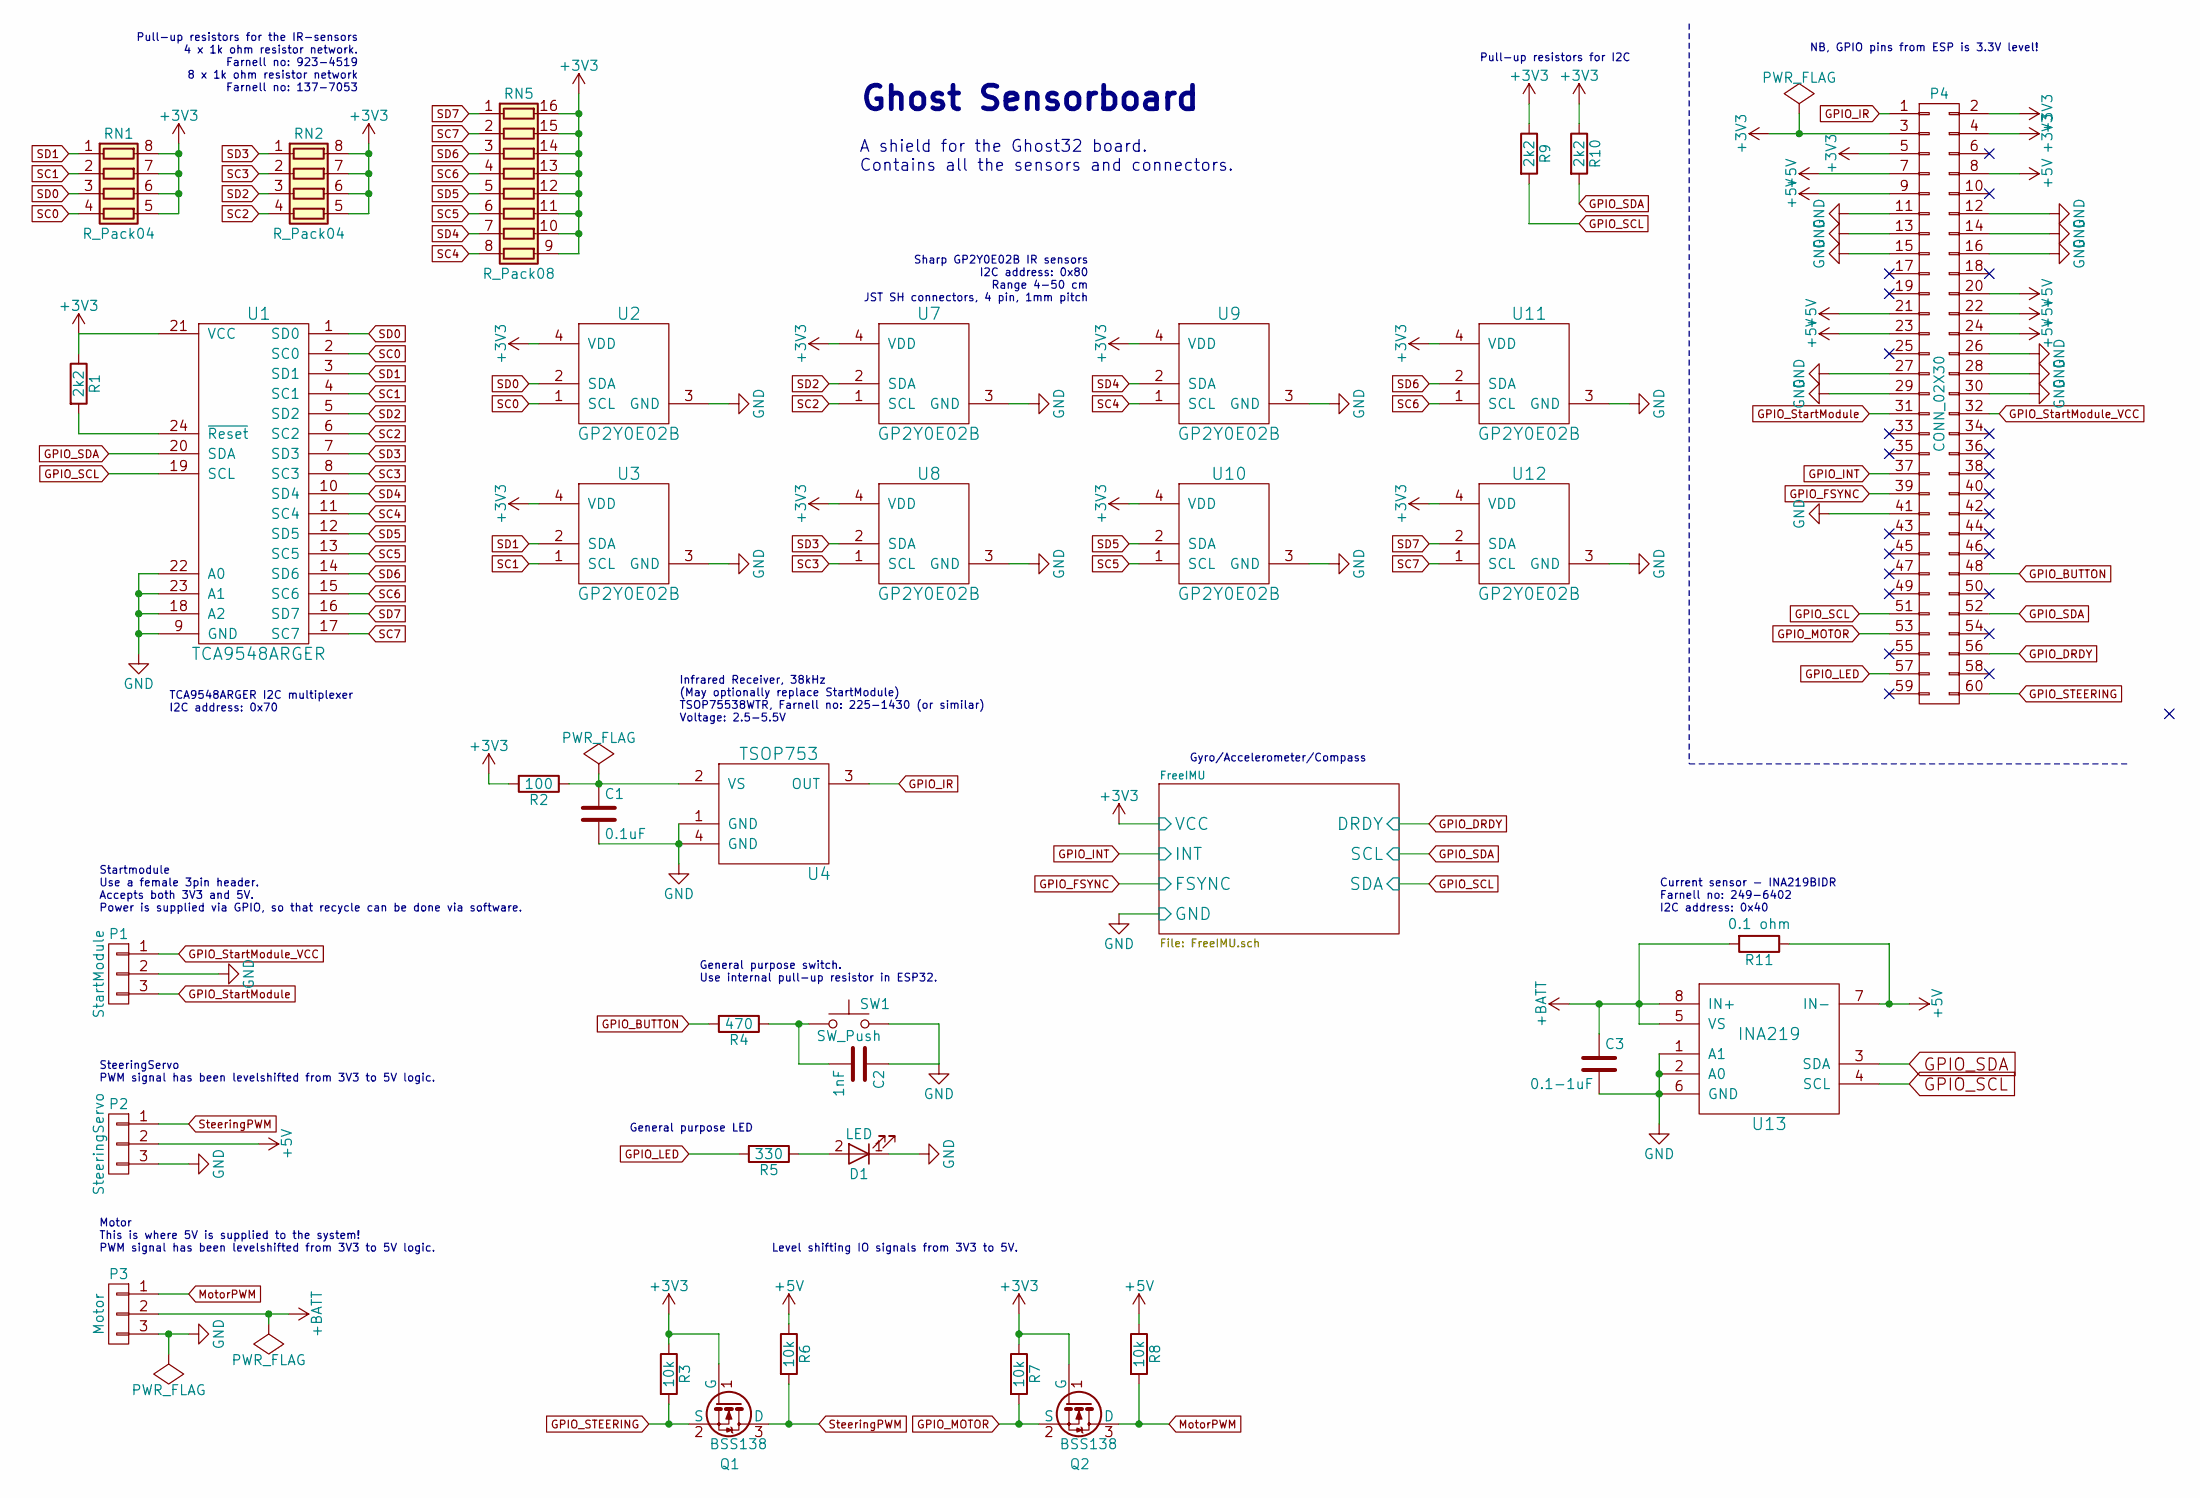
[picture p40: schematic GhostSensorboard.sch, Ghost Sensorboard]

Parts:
C1: 0.1uF; C_0603
C2: 1nF; C_0603
C3: 0.1-1uF; C_0603
D1: LED; LED_0805
P1: StartModule; Pin_Header_Straight_1x03_Pitch2.54mm
P2: SteeringServo; Pin_Header_Straight_1x03_Pitch2.54mm
P3: Motor; Pin_Header_Straight_1x03_Pitch2.54mm
P4: CONN_02X30; hrs-fx8c-60s-sv
Q1, Q2: BSS138; SOT-23
R1, R9, R10: 2k2; R_0603_HandSoldering
R2: 100; R_0603_HandSoldering
R3, R6, R7, R8: 10k; R_0603_HandSoldering
R4: 470; R_0603_HandSoldering
R5: 330; R_0603_HandSoldering
R11: 0.1 ohm; R_0603_HandSoldering
RN1, RN2: R_Pack04; R_Array_Convex_4x0603
RN5: R_Pack08; R_Array_Convex_8x0602
SW1: SW_Push; SW_SPST_EVQP2
U1: TCA9548ARGER; QFN-24_4x4mm_Pitch0.5mm
U2, U3, U7, U8, U9, U10, U11, U12: GP2Y0E02B; JST_SH_BM04B-SRSS-TB_04x1.00mm_Straight
U4: TSOP753; TSOP75x
U13: INA219; SOIC-8-N

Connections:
+3V3: P4.2, P4.3, P4.4, P4.5, Q1.1 (G), Q2.1 (G), R1.1, R2.2, R3.1, R7.1, R9.1, R10.1, RN1.5 (R4.2), RN1.6 (R3.2), RN1.7 (R2.2), RN1.8 (R1.2), RN2.5 (R4.2), RN2.6 (R3.2), RN2.7 (R2.2), RN2.8 (R1.2), RN5.9 (R8.2), RN5.10 (R7.2), RN5.11 (R6.2), RN5.12 (R5.2), RN5.13 (R4.2), RN5.14 (R3.2), RN5.15 (R2.2), RN5.16 (R1.2), U1.21 (VCC), U2.4 (VDD), U3.4 (VDD), U7.4 (VDD), U8.4 (VDD), U9.4 (VDD), U10.4 (VDD), U11.4 (VDD), U12.4 (VDD); also elsewhere on the board
+5V: P2.2, P4.7, P4.8, P4.9, P4.20, P4.21, P4.22, P4.23, P4.24, R6.1, R8.1, R11.1, U13.7 (IN-)
+BATT: C3.1, P3.2, R11.2, U13.5 (VS), U13.8 (IN+)
GND: C1.2, C2.1, C3.2, D1.1 (K), P1.2, P2.3, P3.3, P4.11, P4.12, P4.13, P4.14, P4.15, P4.16, P4.26, P4.27, P4.28, P4.29, P4.30, P4.41, SW1.2, U1.9 (GND), U1.18 (A2), U1.22 (A0), U1.23 (A1), U2.3 (GND), U3.3 (GND), U4.1 (GND), U4.4 (GND), U7.3 (GND), U8.3 (GND), U9.3 (GND), U10.3 (GND), U11.3 (GND), U12.3 (GND), U13.1 (A1), U13.2 (A0), U13.6 (GND); also elsewhere on the board
GPIO_BUTTON: P4.48, R4.2
GPIO_DRDY: P4.56; also elsewhere on the board
GPIO_FSYNC: P4.39; also elsewhere on the board
GPIO_INT: P4.37; also elsewhere on the board
GPIO_IR: P4.1, U4.3 (OUT)
GPIO_LED: P4.57, R5.2
GPIO_MOTOR: P4.53, Q2.2 (S), R7.2
GPIO_SCL: P4.51, R9.2, U1.19 (SCL), U13.4 (SCL); also elsewhere on the board
GPIO_SDA: P4.52, R10.2, U1.20 (SDA), U13.3 (SDA); also elsewhere on the board
GPIO_STEERING: P4.60, Q1.2 (S), R3.2
GPIO_StartModule: P1.3, P4.31
GPIO_StartModule_VCC: P1.1, P4.32
MotorPWM: P3.1, Q2.3 (D), R8.2
unnamed: C1.1, R2.1, U4.2 (VS)
unnamed: C2.2, R4.1, SW1.1
unnamed: D1.2 (A), R5.1
unnamed: R1.2, U1.24 (~Reset)
SC0: RN1.4 (R4.1), U1.2 (SC0), U2.1 (SCL)
SC1: RN1.2 (R2.1), U1.4 (SC1), U3.1 (SCL)
SC2: RN2.4 (R4.1), U1.6 (SC2), U7.1 (SCL)
SC3: RN2.2 (R2.1), U1.8 (SC3), U8.1 (SCL)
SC4: RN5.8 (R8.1), U1.11 (SC4), U9.1 (SCL)
SC5: RN5.6 (R6.1), U1.13 (SC5), U10.1 (SCL)
SC6: RN5.4 (R4.1), U1.15 (SC6), U11.1 (SCL)
SC7: RN5.2 (R2.1), U1.17 (SC7), U12.1 (SCL)
SD0: RN1.3 (R3.1), U1.1 (SD0), U2.2 (SDA)
SD1: RN1.1 (R1.1), U1.3 (SD1), U3.2 (SDA)
SD2: RN2.3 (R3.1), U1.5 (SD2), U7.2 (SDA)
SD3: RN2.1 (R1.1), U1.7 (SD3), U8.2 (SDA)
SD4: RN5.7 (R7.1), U1.10 (SD4), U9.2 (SDA)
SD5: RN5.5 (R5.1), U1.12 (SD5), U10.2 (SDA)
SD6: RN5.3 (R3.1), U1.14 (SD6), U11.2 (SDA)
SD7: RN5.1 (R1.1), U1.16 (SD7), U12.2 (SDA)
SteeringPWM: P2.1, Q1.3 (D), R6.2

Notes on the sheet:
Ghost Sensorboard
A shield for the Ghost32 board. Contains all the sensors and connectors.
NB, GPIO pins from ESP is 3.3V level!
Startmodule Use a female 3pin header. Accepts both 3V3 and 5V. Power is supplied via GPIO, so that recycle can be done via software.
Pull-up resistors for the IR-sensors 4 x 1k ohm resistor network. Farnell no: 923-4519 8 x 1k ohm resistor network Farnell no: 137-7053
Sharp GP2Y0E02B IR sensors I2C address: 0x80 Range 4-50 cm JST SH connectors, 4 pin, 1mm pitch
SteeringServo PWM signal has been levelshifted from 3V3 to 5V logic.
Motor This is where 5V is supplied to the system! PWM signal has been levelshifted from 3V3 to 5V logic.
Level shifting IO signals from 3V3 to 5V.
Current sensor - INA219BIDR Farnell no: 249-6402 I2C address: 0x40
General purpose switch. Use internal pull-up resistor in ESP32.
Infrared Receiver, 38kHz (May optionally replace StartModule) TSOP75538WTR, Farnell no: 225-1430 (or similar) Voltage: 2.5-5.5V
Pull-up resistors for I2C
General purpose LED
Gyro/Accelerometer/Compass
TCA9548ARGER I2C multiplexer I2C address: 0x70

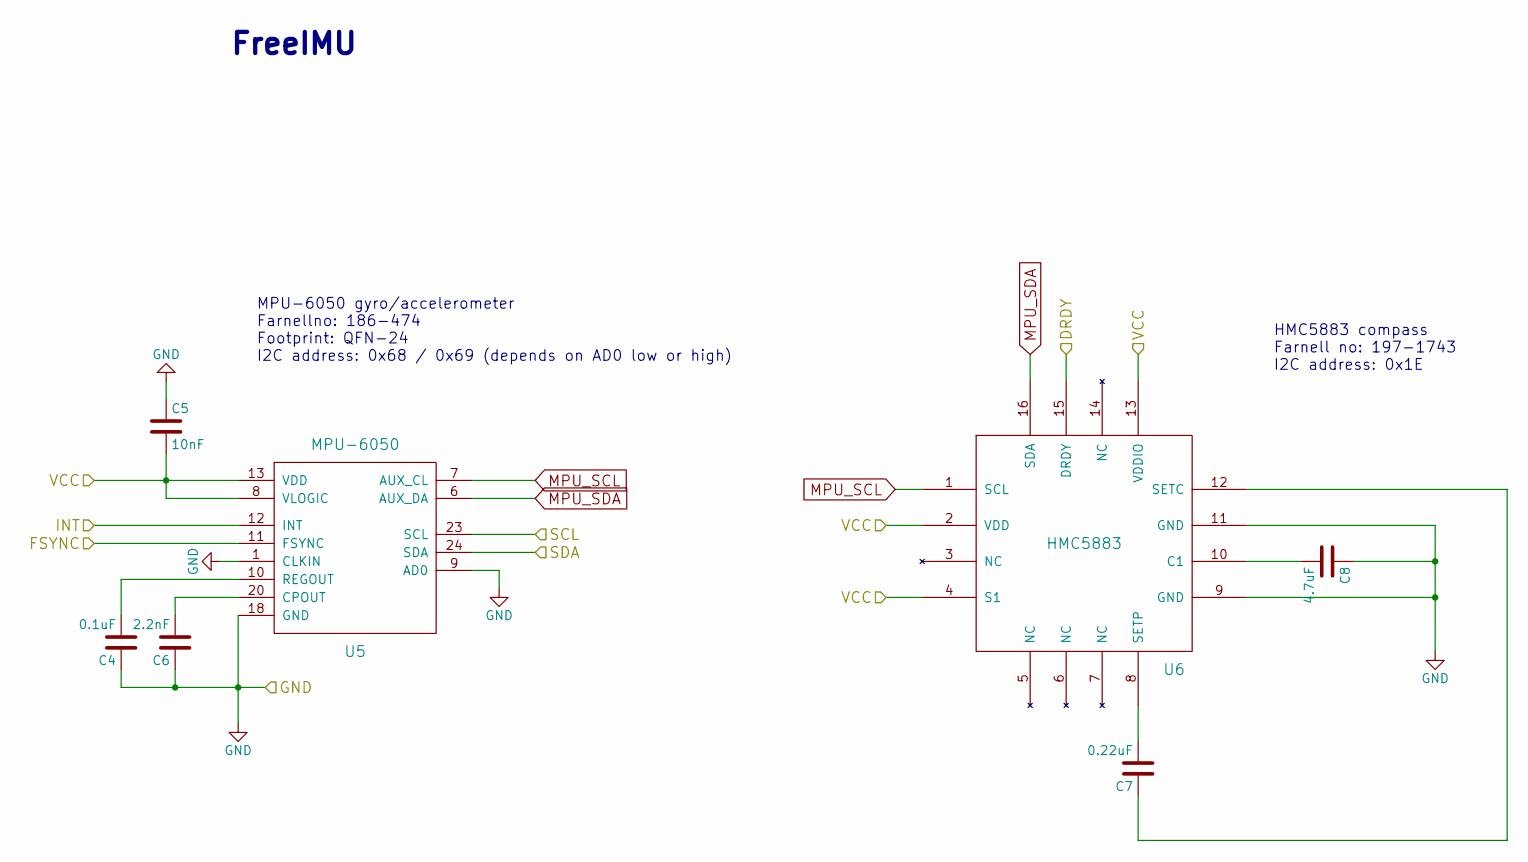
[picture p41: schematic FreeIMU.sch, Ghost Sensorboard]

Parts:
C4: 0.1uF; C_0603
C5: 10nF; C_0603
C6: 2.2nF; C_0603
C7: 0.22uF; C_0603
C8: 4.7uF; C_0603
U5: MPU-6050; QFN-24-1EP_4x4mm_Pitch0.5mm
U6: HMC5883

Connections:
+3V3: C5.2, U5.8 (VLOGIC), U5.13 (VDD), U6.2 (VDD), U6.4 (S1), U6.13 (VDDIO); also elsewhere on the board
GND: C4.1, C5.1, C6.1, C8.1, U5.1 (CLKIN), U5.9 (AD0), U5.18 (GND), U6.9 (GND), U6.11 (GND); also elsewhere on the board
GPIO_DRDY: U6.15 (DRDY); also elsewhere on the board
GPIO_FSYNC: U5.11 (FSYNC); also elsewhere on the board
GPIO_INT: U5.12 (INT); also elsewhere on the board
GPIO_SCL: U5.24 (SDA); also elsewhere on the board
GPIO_SDA: U5.23 (SCL); also elsewhere on the board
MPU_SCL: U5.7 (AUX_CL), U6.1 (SCL)
MPU_SDA: U5.6 (AUX_DA), U6.16 (SDA)
unnamed: C4.2, U5.10 (REGOUT)
unnamed: C6.2, U5.20 (CPOUT)
unnamed: C7.1, U6.12 (SETC)
unnamed: C7.2, U6.8 (SETP)
unnamed: C8.2, U6.10 (C1)

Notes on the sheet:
MPU-6050 gyro/accelerometer Farnellno: 186-474 Footprint: QFN-24 I2C address: 0x68 / 0x69 (depends on AD0 low or high)
FreeIMU
HMC5883 compass Farnell no: 197-1743 I2C address: 0x1E


Board: 2 copper layers, 50.0 x 50.0 mm, 43 parts (1 on the bottom side), 45 nets.

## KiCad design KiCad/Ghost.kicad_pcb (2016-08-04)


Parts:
C1: 0.1-1uF; C_0603
C2: 470pF; C_0603
C3: 2.2uF; C_0603
C9: 100nF; C_0603
D1: GREEN; LED_0603
D2: ACT; LED_0603
D3: RED; LED_0603
P1: MOTOR; Pin_Header_Straight_1x03
P2: SERVO; Pin_Header_Straight_1x03
P3: START; Pin_Header_Straight_1x03
P4: CONN_01X06; Pin_Header_Straight_1x06
P5: RGB; Pin_Header_Straight_1x03
Q1: MMBT3904; SOT-23
R1: 0.1ohm; R_0603
R2, R3: 2k2; R_0603
R4: 40; R_0603
R5: 100; R_0603
R6: 220; R_0603
R7: 50; R_0603
R9: 0; R_0603
R25: 270; R_0603
R26: 10k; R_0603
R28, R29, R30: 3k3; R_0603
SW1: BTN1; SW_SPST_SKQG
SW2: PROG; SW_SPST_SKQG
U1: INA219; SOIC-8_3.9x4.9mm_Pitch1.27mm
U2: Teensy31_32; Teensy-3.1_3.2
U3: MIC5219-3.3YM5; SOT-23-5
U4: HM-11
U16: Transmissive_Photo_Interrupter; Pin_Header_Straight_1x04
U17: ESP8266_ESP-12; ESP8266_ESP_12E

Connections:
+3V3: C3.1, C9.2, R2.1, R3.2, R28.1, R29.1, U3.5 (OUT), U4.9 (VCC), U4.11 (~RESET), U17.8 (VCC); also elsewhere on the board
+5V: P2.2, P5.3, R1.1, R5.1, R9.1, R25.2, R26.2, U1.7 (IN-), U2.26 (VIN), U3.1 (VIN), U3.3 (Enable)
+BATT: C1.1, P1.2, R1.2, U1.5 (VS), U1.8 (IN+)
BLUETOOTH_RX: U2.1 (TX1), U4.4 (UART_RX)
BLUETOOTH_TX: U2.0 (RX1), U4.2 (UART_TX)
BUTTON: SW1.1, U2.7 (RX3)
ENCODER: R26.1, U2.17 (A3/PWM), U16.3 (COLLECTOR)
GND: C1.2, C2.2, C3.2, C9.1, D3.1 (K), P1.1, P2.1, P3.2, P4.1, P5.1, Q1.2 (E), R6.2, R30.1, SW1.2, SW2.2, U1.1 (A1), U1.2 (A0), U1.6 (GND), U2.25 (GND), U2.27 (GND), U2.34 (GND), U3.2 (GND), U4.12 (GND), U16.2 (CATHODE), U16.4 (EMITTER), U17.15 (GND); also elsewhere on the board
IMU_DRDY: U2.21 (A7); also elsewhere on the board
IMU_FSYNC: U2.23 (A9/PWM); also elsewhere on the board
IMU_INT: U2.22 (A8/PWM); also elsewhere on the board
MOTOR: P1.3, U2.3 (PWM)
unnamed: C2.1, U3.4 (BYP)
unnamed: D1.1 (K), R4.2
unnamed: D2.1 (K), R6.1
unnamed: D2.2 (A), U4.15 (PIO1)
unnamed: D3.2 (A), R7.1
unnamed: P4.3, R9.2
unnamed: Q1.1 (B), R4.1
unnamed: Q1.3 (C), R5.2, R7.2
unnamed: R25.1, U16.1 (ANODE)
unnamed: R28.2, SW2.1, U17.18 (GPIO0)
unnamed: R29.2, U17.17 (GPIO2)
unnamed: R30.2, U17.16 (GPIO15)
RGB_STRIP: P5.2, U2.12 (MISO0)
START: P3.3, U2.5 (MISO)
START_POWER: P3.1, U2.6 (PWM)
STEERING: P2.3, U2.4 (PWM)
TEENSY_SCL: R2.2, U1.4 (SCL), U2.19 (A5); also elsewhere on the board
TEENSY_SDA: R3.1, U1.3 (SDA), U2.18 (A4); also elsewhere on the board
TOGGLE_LED: D1.2 (A), U2.2 (D2)
WIFI_ENABLE: U2.8 (TX3), U17.3 (EN)
WIFI_RX: P4.4, U2.10 (TX2), U17.21 (RXD0)
WIFI_TX: P4.5, U2.9 (RX2), U17.22 (TXD0)
~WIFI_RESET: U2.11 (MOSI0), U17.1 (RST)

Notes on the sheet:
GHOST (rev 2)
Current sensor - INA219BIDR Farnell: 2496402 I2C addr: 0x40
MIC5219 3.3V LDO regulator (max 500mA out)
Toggle LEDs with one GPIO NPN is a MMBT3904, SOT-23.
Motor is a Hobbyking XC-10A ESC (Product ID: 913000001) It has a 5V regulator onboard which supplies the PCB with power. 3 pin connector is thus a power-input, but also used for PWM controlling motor.
Steering can be a SG-90 microservo.
Start is from Startmodule.com. NB, use female header. Can be power-cycled from Teensy VCC: 3.3-5V
General purpose switch. Google 'Teensy Input with Pullup' for code.
WS2812 LED strip NB, each LED can draw up to 60mA
Bluetooth, HM-11 VCC: 2.5 - 3.7 Pull Reset-pin to ground for 5ms to reset. http://www.seeedstudio.com/wiki/Bluetooth_V4.0_HM-11_BLE_Module http://lightlogproject.org/blog/tag/hm-11/
KTIR0611S Used to detect rotations of main drive shaft
WiFi. Can be enabled/disabled from Teensy. Use pushbutton for firmware programming. NB, pull ~Reset~=HIGH and Enable=HIGH using Teensy.
Programming header for ESP8266 Use FTDI Basic. 0 ohm resistor acts as optional jumper for power.


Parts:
C4: 0.1uF; C_0603
C5: 10nF; C_0603
C6: 2.2nF; C_0603
C7: 0.22uF; C_0603
C8: 4.7uF; C_0603
U5: MPU-6050; QFN-24-1EP_4x4mm_Pitch0.5mm
U6: HMC5883; QFN-16-1EP_3x3mm_Pitch0.5mm

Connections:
+3V3: C5.2, U5.8 (VLOGIC), U5.13 (VDD), U6.2 (VDD), U6.4 (S1), U6.13 (VDDIO); also elsewhere on the board
GND: C4.1, C5.1, C6.1, C8.1, U5.1 (CLKIN), U5.9 (AD0), U5.18 (GND), U6.9 (GND), U6.11 (GND); also elsewhere on the board
IMU_DRDY: U6.15 (DRDY); also elsewhere on the board
IMU_FSYNC: U5.11 (FSYNC); also elsewhere on the board
IMU_INT: U5.12 (INT); also elsewhere on the board
MPU_SCL: U5.7 (AUX_CL), U6.1 (SCL)
MPU_SDA: U5.6 (AUX_DA), U6.16 (SDA)
unnamed: C4.2, U5.10 (REGOUT)
unnamed: C6.2, U5.20 (CPOUT)
unnamed: C7.1, U6.12 (SETC)
unnamed: C7.2, U6.8 (SETP)
unnamed: C8.2, U6.10 (C1)
TEENSY_SCL: U5.23 (SCL); also elsewhere on the board
TEENSY_SDA: U5.24 (SDA); also elsewhere on the board

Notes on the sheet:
MPU-6050 (Farnell: 186474, QFN-24) I2C address: 0x68 / 0x69 (depends on AD0 low or high)
FreeIMU

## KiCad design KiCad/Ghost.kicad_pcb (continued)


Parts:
R8: 2k2; R_0603
RP1, RP2, RP3, RP4: 4 x 1k ohm; R_Array_Convex_4x0603
U7: TCA9548ARGER; QFN-24-1EP_4x4mm_Pitch0.5mm
U8, U9, U10, U11, U12, U13, U14, U15: GP2Y0E02B; JST_SH_BM04B-SRSS-TB_04x1.00mm_Straight

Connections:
+3V3: R8.1, RP1.1, RP1.2, RP1.3, RP1.4, RP2.1, RP2.2, RP2.3, RP2.4, RP3.1, RP3.2, RP3.3, RP3.4, RP4.1, RP4.2, RP4.3, RP4.4, U7.21 (VCC), U8.4 (VDD), U9.4 (VDD), U10.4 (VDD), U11.4 (VDD), U12.4 (VDD), U13.4 (VDD), U14.4 (VDD), U15.4 (VDD); also elsewhere on the board
/IRSensors/SCL_0: RP1.8 (R1), U7.2 (SC0), U8.1 (SCL)
/IRSensors/SCL_1: RP1.6 (R3), U7.4 (SC1), U9.1 (SCL)
/IRSensors/SCL_2: RP2.8 (R1), U7.6 (SC2), U10.1 (SCL)
/IRSensors/SCL_3: RP2.6 (R3), U7.8 (SC3), U11.1 (SCL)
/IRSensors/SCL_4: RP3.8 (R1), U7.11 (SC4), U12.1 (SCL)
/IRSensors/SCL_5: RP3.6 (R3), U7.13 (SC5), U13.1 (SCL)
/IRSensors/SCL_6: RP4.8 (R1), U7.15 (SC6), U14.1 (SCL)
/IRSensors/SCL_7: RP4.6 (R3), U7.17 (SC7), U15.1 (SCL)
/IRSensors/SDA_0: RP1.7 (R2), U7.1 (SD0), U8.2 (SDA)
/IRSensors/SDA_1: RP1.5 (R4), U7.3 (SD1), U9.2 (SDA)
/IRSensors/SDA_2: RP2.7 (R2), U7.5 (SD2), U10.2 (SDA)
/IRSensors/SDA_3: RP2.5 (R4), U7.7 (SD3), U11.2 (SDA)
/IRSensors/SDA_4: RP3.7 (R2), U7.10 (SD4), U12.2 (SDA)
/IRSensors/SDA_5: RP3.5 (R4), U7.12 (SD5), U13.2 (SDA)
/IRSensors/SDA_6: RP4.7 (R2), U7.14 (SD6), U14.2 (SDA)
/IRSensors/SDA_7: RP4.5 (R4), U7.16 (SD7), U15.2 (SDA)
GND: U7.9 (GND), U7.18 (A2), U7.22 (A0), U7.23 (A1), U8.3 (GND), U9.3 (GND), U10.3 (GND), U11.3 (GND), U12.3 (GND), U13.3 (GND), U14.3 (GND), U15.3 (GND); also elsewhere on the board
unnamed: R8.2, U7.24 (~Reset)
TEENSY_SCL: U7.19 (SCL); also elsewhere on the board
TEENSY_SDA: U7.20 (SDA); also elsewhere on the board

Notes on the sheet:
JST SH connectors, 4 pin, 1mm pitch
Pull-up resistors for I2C. Using resistor array to save board space. Farnell partno: 924-1213
I2C multiplexer TCA9548ARGER Farnell partno: 249-6588


Board: 2 copper layers, 80.0 x 49.0 mm, 55 parts (0 on the bottom side), 59 nets.

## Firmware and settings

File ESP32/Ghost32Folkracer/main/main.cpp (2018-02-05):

/*
 * 1. Open up the project properties
 * 2. Visit C/C++ General > Preprocessor Include Paths, Macros, etc
 * 3. Select the Providers tab
 * 4. Check the box for "CDT GCC Built-in Compiler Settings"
 * 5. Set the compiler spec command to "xtensa-esp32-elf-gcc ${FLAGS} -E -P -v -dD "${INPUTS}""
 * 6. Rebuild the index
 */

#include <esp_log.h>
#include <string>
#include "sdkconfig.h"
#include "driver/gpio.h"
#include "freertos/FreeRTOS.h"
#include "freertos/task.h"
#include "freertos/queue.h"
#include "TaskMotor.cpp"
#include "TaskDriveController.cpp"
#include "TaskStartModule.cpp"
#include "StartModule.h"
#include "Sensors/IRSensor.h"
#include "Sensors/TCA9548.h"
#include "pid.h"
//#include "Sensors/IRSensorConfig.h"
#include "VectorCalculator.h"
#include "MovementDetector.h"
#include "Sensors/MPU6050.h"
#include <cmath>

#define MOTOR_PIN GPIO_NUM_26
#define STEERING_PIN GPIO_NUM_27

#define SDA_PIN GPIO_NUM_13 //33
#define SCL_PIN GPIO_NUM_14 //32

//#undef ESP_ERROR_CHECK
//#define ESP_ERROR_CHECK(x)   do { esp_err_t rc = (x); if (rc != ESP_OK) { ESP_LOGE("err", "esp_err_t = %d", rc); assert(0 && #x);} } while(0);

static char tag[] = "Ghost32";

extern "C" {
void app_main(void);
}

//Global variables
int state_motor_speed = 0;
int global_state_startmodule = eStartModuleState::WAITING;
QueueHandle_t queue_startmodule;
QueueHandle_t queue_sensorvalues;
QueueHandle_t queue_actuators;

//Configuration
bool useWallCompensation = true;
bool doubleSpeedWhenUsingWallCompensation = false; //Double speed if we're driving parallell to wall.
bool useCrashSensing = true; 	//If we're about to hit a wall, then perform quick turn.
bool useReverseOnCrash = true; //If up-close to wall in front, then reverse.
int defaultSpeed = 17;
//Cofnfiguration end

struct movement_t {
	int speed;
	eDirection direction;
	int steering_angle;
	//bool enabled;
};

struct sensorvalues_t {
	int sensor0;
	int sensor1;
	int sensor2;
	int sensor3;
	int sensor4;
	int sensor5;
	int sensor6;
	int sensor7;
	int sensor8;
	int sensor9;
	int sensor10;
	int sensor11;
	int sensor12;
	int sensor13;
	int sensor14;
	int sensor15;
	int compass;
	int irdata[16];
};

//extern struct accelerometer_data {
//	int x;
//	int y;
//	int z;
//};

void task_listener(void *parameters) {
	int x = 89;
	//BaseType_t driverTask;
	//BaseType_t actuatorTask;

	while (true) {
		ESP_LOGW(tag, "Listening on queue_startmodule...");
		BaseType_t rc = xQueueReceive(queue_startmodule, &x, portMAX_DELAY);
		ESP_LOGW(tag, "queue_startmodule said %d", rc);

		//movement_t m;
		//m.enabled = true;
		//xQueueSend(queue_actuators, &m, 0);

//		if (x == 1)
//		{
//			driverTask = xTaskCreate(task_drivecomputer, "Driver task", 4096, NULL, 4, NULL);
//		    actuatorTask = xTaskCreate(task_actuators, "Actuators task", 4096, NULL, 5, NULL);
//		}
//		else
//		{
//			vTaskDelete(driverTask);
//			vTaskDelete(actuatorTask);
//		}
	}
}

void task_irsensors(void *p) {
	ESP_LOGI(tag, "task_irsensors started");

	Sensors::TCA9548 tca9548;
	//esp_err_t result =
	tca9548.setChannel(1);

	Sensors::IRSensorConfig irsensor_conf;
	irsensor_conf.mounting_angle = 45.0;
	irsensor_conf.offset_x_mm = 20.0;
	irsensor_conf.offset_y_mm = 9.5;

	Sensors::IRSensor irsensor(irsensor_conf);

	while (true) {
//		ESP_LOGI(tag, "IRSensors loop");
//		int left, right = 0;
//
//		tca9548.setChannel(0);
//		left = irsensor.getDistance();
		//ESP_LOGI(tag, "Left: %d", left);

//		tca9548.setChannel(1);
//		right = irsensor.getDistance();
		//ESP_LOGI(tag, "Right: %d", right);
//
//		int angle = 0;
//		if (left > right)
//			angle = 3000;
//		//steering.TurnTo(3000);
//		else
//			angle = 2200;
//		//steering.TurnTo(2200);
		//ESP_LOGI(tag, "Angle %d", angle);

		sensorvalues_t data;
		//data.compass = 300;
		//data.sensor0 = 30;
		//data.sensor1 = 20; //....

		//movement_t m;
		//m.speed = 100;
		//m.steering_angle = angle;

		//Loop over all the 16 IR sensors, and get the distances.
		for (int channel = 0; channel <= 15; channel++) {
			tca9548.setChannel(channel);
			data.irdata[channel] = irsensor.getDistance();
		}

		//xQueueSend(queue_actuators, &m, NULL);
		xQueueSend(queue_sensorvalues, &data, 0);

		vTaskDelay(pdMS_TO_TICKS(10));
	}

	vTaskDelete(NULL);
}

void task_drivecomputer(void *p) {
	ESP_LOGI(tag, "task_drivecomputer started");

	Sensors::MovementDetector movementDetector;

	Sensors::MPU6050 mpu6050;

	//Wait for StartModule

//	int x = 123;
//	//BaseType_t rc = xQueueReceive(queue_startmodule, &x, portMAX_DELAY);
//	ESP_LOGI(tag, "Drivecomputer waiting for Startmodule");
//	while (x != 1)
//	{
//		BaseType_t rc = xQueueReceive(queue_startmodule, &x, 0);
//	}

	while (true) {
		if (global_state_startmodule == eStartModuleState::WAITING
				|| global_state_startmodule == eStartModuleState::STOPPED) {
			movement_t m;
			m.speed = 0;
			m.steering_angle = 50;
			xQueueSend(queue_actuators, &m, 0);
			//continue;
		} else if (global_state_startmodule == eStartModuleState::RUNNING) {

			//ESP_LOGI(tag, "DriveComputer loop");

   		Sensors::accelerometer_data acc = mpu6050.Read();
			ESP_LOGI(tag, "X: %d", acc.x);
			ESP_LOGI(tag, "Y: %d", acc.y);
			ESP_LOGI(tag, "Z: %d", acc.z);

			//Listen for incoming sensor-data
			sensorvalues_t data;
			if (xQueueReceive(queue_sensorvalues, &data, portMAX_DELAY)
					== pdPASS) {

				movement_t m;

				int left1 = data.irdata[4];
				int right1 = data.irdata[1];
				int left2 = data.irdata[0];
				int right2 = data.irdata[5];
				ESP_LOGI(tag, "Left1: %d", left1);
				ESP_LOGI(tag, "Left2: %d", left2);
				ESP_LOGI(tag, "Right1: %d", right1);
				ESP_LOGI(tag, "Right2: %d", right2);

				int leftTotal = left1 + left2;
				int rightTotal = right1 + right2;
				//ESP_LOGI(tag, "LeftTotal: %d", leftTotal);
				//ESP_LOGI(tag, "RightTotal: %d", rightTotal);

				int percent = (leftTotal * 100 / (rightTotal + leftTotal));
				m.steering_angle = percent;

				//Start calculating angle to wall

				float angleToWall = 0.0;
				if (useWallCompensation) {
					VectorCalculator calc;
					Point p1 = calc.FindPointFromAngleAndDistance(60, left1);
					//Compensate for X/Y offset sensor positions
					p1.x = p1.x - 5.2;
					p1.y = p1.y + 2.8;
					Point p2 = calc.FindPointFromAngleAndDistance(25, left2);
					Point vWall = calc.SubtractPoints(p2, p1);
					Point
					vCar = {x: 1, y:0};
					angleToWall = calc.GetAngleBetweenVectors(vCar, vWall);
					angleToWall = angleToWall * 180.0 / M_PI; //From radians to degrees
					if (vWall.y < 0)
						angleToWall *= -1;
					float wallAngleCompensation = 1.0; //1.0 is keep as is.
					if (angleToWall > 45)
						wallAngleCompensation = 0.5;
					if (angleToWall < -45)
						wallAngleCompensation = 1.5;
					m.steering_angle *= wallAngleCompensation;
					ESP_LOGI(tag, "Angle to wall: %0.2f", angleToWall);
				}
				//End calculating angle to wall

				//Speed - set default speed and direction
				m.speed = defaultSpeed;
				m.direction = FORWARD;

				//Standing still? Then stop the motor.
//				std::vector<int> s;
//				s.assign(data.irdata, data.irdata+16);
//				movementDetector.SaveIRSensorReadings(s);
//				if (movementDetector.IsStandingStill())
//				{
//					ESP_LOGW(tag, "NO MOTION DETECTED!");
//					m.speed = 0;
//				}

				//Adjust speed (go twice as fast if we are parallell to the wall)
				if (useWallCompensation
						&& doubleSpeedWhenUsingWallCompensation) {
					if (abs(angleToWall) < 10)
						m.speed *= 2;
				}

				//About to crash, make big turn!
				if (useCrashSensing) {
					if (left2 < 20 && right2 < 20) {
						if (m.steering_angle > 50)
							m.steering_angle *= 2; //= 100;
						else
							m.steering_angle /= 2; // 0;
					}
				}

				//Crashed into wall
				if (useReverseOnCrash) {
					if (left2 < 10 && right2 < 10) {
						m.speed = 50;
						m.direction = BACKWARD;
						m.steering_angle = 0; //*= -2;
					}
				}

				//TODO, add PID controller?

				//Send the desired actuator movements to the queue.
				xQueueSend(queue_actuators, &m, 0);
			}
		}

		vTaskDelay(pdMS_TO_TICKS(10));
	}

	vTaskDelete(NULL);
}

void task_actuators(void *p) {
	ESP_LOGI(tag, "task_actuators started");

	int min = 2000;
	int max = 4100;
	ServoSteering steering(STEERING_PIN, min, max);
	Motor motor(MOTOR_PIN, 1800, 3400);
	motor.calibrate();

	while (true) {
		ESP_LOGI(tag, "Actuators loop");
		movement_t m;
		//ESP_LOGI(tag, "task_actuators waiting for steering command...");

		//Startmodule
//		int x = 0;
//		if (xQueueReceive(queue_startmodule, &x, portMAX_DELAY) == pdPASS) {
//			ESP_LOGI(tag, "Startmodule toggling motors: %d", x);
//			//motor.ToggleEnable();
//		}

		//Wait for an incoming command telling us to change motorspeed, or turn the wheels.
		if (xQueueReceive(queue_actuators, &m, portMAX_DELAY) == pdPASS) {
			ESP_LOGI(tag, "TurnTo(%d)", m.steering_angle);
			//motor.SetEnable(true);
			ESP_LOGI(tag, "Steering angle: %d", m.steering_angle);
			steering.TurnTo(m.steering_angle);
			motor.SetDirection(m.direction);
			motor.SetSpeed(m.speed);
			ESP_LOGI(tag, "SetSpeed(%d)", m.speed);
		}
		vTaskDelay(pdMS_TO_TICKS(10));
	}

	vTaskDelete(NULL);
}

void app_main(void) {

	/*
	 * Configure I2C
	 */
	i2c_config_t conf;
	conf.mode = I2C_MODE_MASTER;
	conf.sda_io_num = SDA_PIN;
	conf.scl_io_num = SCL_PIN;
	conf.sda_pullup_en = GPIO_PULLUP_ENABLE;
	conf.scl_pullup_en = GPIO_PULLUP_ENABLE;
	conf.master.clk_speed = 1000000;
	i2c_param_config(I2C_NUM_0, &conf);
	i2c_driver_install(I2C_NUM_0, I2C_MODE_MASTER, 0, 0, 0);

	/*
	 * Create Queues
	 *
	 * TODO -  describe what queues are used for...
	 */

	int queue_size_startmodule = 1;
	queue_startmodule = xQueueCreate(queue_size_startmodule, sizeof(int));
	queue_sensorvalues = xQueueCreate(1, sizeof(sensorvalues_t));
	queue_actuators = xQueueCreate(1, sizeof(movement_t));

	/*
	 * Create Tasks
	 *
	 * The lowest priority tasks gather sensorvalues, and passes them to higher level
	 * task which processes the data. Then that task sends drive instructions to even higher
	 * level tasks which manipulates actuators (steering and motor).
	 *
	 * IRSensors -> array of distances -> DriveComputer
	 * Compass -> heading -> DriveComputer
	 * DriveComputer -> Motor
	 * DriveComputer -> Steering
	 */

	xTaskCreate(task_startmodule, "Startmodule task", 4096, NULL, 2, NULL);
	xTaskCreate(task_irsensors, "IRSensors", 4096, NULL, 3, NULL);
	//xTaskCreate(task_listener, "Listener", 4096, NULL, 2, NULL);
	xTaskCreate(task_drivecomputer, "Driver task", 4096, NULL, 4, NULL);
	xTaskCreate(task_actuators, "Actuators task", 4096, NULL, 5, NULL);

	for (;;) {
		vTaskDelay(pdMS_TO_TICKS(1000));
	}

	//Experimenting below...

	//Motor motor(MOTOR_PIN, 1800, 3400);
	//motor.calibrate();

	//ServoSteering steering(STEERING_PIN, 2000, 4100);

	//Sensors::TCA9548 tca9548;
	//esp_err_t result = tca9548.setChannel(1);
	//ESP_LOGD(tag, "TCA9548 channel result: %d", result);
	//ESP_ERROR_CHECK(result);

	//IRSensorArray irsensors();
	//int readings[16] = irsensors.getDistances();

	//double mounting_angle = 45.0;

//	Sensors::IRSensorConfig irsensor_conf;
//	irsensor_conf.mounting_angle = 45.0;
//	irsensor_conf.offset_x_mm = 20.0;
//	irsensor_conf.offset_y_mm = 9.5;
//
//	Sensors::IRSensor irsensor(irsensor_conf);
	//esp_err_t irsensor_found = irsensor.detectDevice();
	//if (irsensor_found != ESP_OK)
	//	ESP_LOGE(tag, "Unable to detect IRSensor");

	//Compass compass();
	//int heading = compass.read();

	//LED l(GPIO_NUM_23);
	//l.Blink(200);

//	for (;;) {
//		if (global_state_startmodule == eStartModuleState::WAITING) {
//			ESP_LOGD(tag, "In WAITING state");
//			motor.SetSpeed(0);
//			//steering.TurnTo(2200);
//			int cm = irsensor.getDistance();
//			ESP_LOGD(tag, "Distance: %d", cm);
//			//printf("[W] CM: %d\n", cm);
//		} else if (global_state_startmodule == eStartModuleState::RUNNING) {
//			//ESP_LOGD(tag, "In RUNNING state");
//			//motor.SetSpeed(3000);
//
//			int left, right = 0;
//
//			tca9548.setChannel(0);
//			left = irsensor.getDistance();
//			//ESP_LOGI(tag, "Left: %d", left);
//
//			tca9548.setChannel(1);
//			right = irsensor.getDistance();
//			//ESP_LOGI(tag, "Right: %d", right);
//
//			if (left > right)
//				steering.TurnTo(3000);
//			else
//				steering.TurnTo(2200);
//
//		} else if (global_state_startmodule == eStartModuleState::STOPPED) {
//			//ESP_LOGD(tag, "In STOPPED state");
//			motor.SetSpeed(1500);
//			steering.TurnTo(4000);
//		}
//
//		vTaskDelay(100 / portTICK_PERIOD_MS);
//	}
}

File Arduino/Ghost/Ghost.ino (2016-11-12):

/*
 * Ghost - folkracer for Stockholm 2016
 * Frode Lillerud
 */

#include <Servo.h>
#include <Wire.h>
#include <PID_v1.h>
#include "Car.h"
extern "C"
{
  #include "utility/twi.h"
}

enum startmoduleStates {
  WAITING,
  RUNNING,
  STOPPED
};

const int STARTMODULE_PIN = 5;
volatile startmoduleStates startmodule_state = WAITING;

const int FRONT_DISTANCE = 25;
const int CRASH_DISTANCE = 10;

bool Debug = false;
bool MotorDisabled = false;

//PID regulator
//double Setpoint, Input, Output;
//double Kp = 2, Ki = 5, Kd = 1;
//PID pid(&Input, &Output, &Setpoint, Kp, Ki, Kd, DIRECT);

//Servo related variables
int servoPin = 4;
Servo steering;
int motorPin = 3;
Servo motor;

const int LED_PIN = 13;

Car car(STARTMODULE_PIN, LED_PIN);

void Trace(const String& message)
{
  Serial.println(message);
}

void TraceNoLine(const String& message)
{
  Serial.print(message);
}

void setup() {
  Serial.begin(115200);
  Trace("Serial OK");

  Serial.println("Configuring steering");
  steering.attach(servoPin); 
  steering.write(130); //ca middle

  //Startmodule
  Serial.println("Configuring StartModule");
  pinMode(STARTMODULE_PIN, INPUT);
  attachInterrupt(STARTMODULE_PIN, changeStartmoduleState, CHANGE);
  startmodule_state = WAITING;

  Serial.println("Configuring I2C and sensors");
  Wire.begin();
  delay(1000);
  setActiveSensor(1);
  setupIRSensors(); 
  
  //PID
  /*Serial.println("Configuring PID");
  Input = 50.0;
  Setpoint = 50.0;
  Kp = 10.0; //5
  Ki = 0.1; //0
  Kd = 10000; //2
  pid.SetOutputLimits(95, 180); //
  pid.SetSampleTime(20); //ms
  pid.SetControllerDirection(REVERSE);
  pid.SetTunings(Kp, Ki, Kd);
  pid.SetResolution(MICROS);
  pid.SetMode(AUTOMATIC);
*/
  Serial.println("Configuring motor");
  motor.attach(motorPin);
  calibrateXC10A();

  //Configure Car
  //car.stop();

  Serial.print("Setup done");
}

elapsedMicros elapsed;

void loop() {

  if (startmodule_state == WAITING)
  {
    //Serial.print("WAITING");
  }
  else if (startmodule_state == RUNNING)
  {
    //Get value from sensors
    int center = getSensorDistanceInCm(0);
    int left = getSensorDistanceInCm(1);
    int right = getSensorDistanceInCm(7);
  
    //NOT PID
    int pos = (right*100 / (right+left)); //Gives a value between 0 and 100.
  
    //PID
    //Input = (right*100.0 / (right+left));
    //pid.Compute();
  
    //Serial.print(left);
    //Serial.print(",");
    //Serial.println(right);
  
    //Figure out where to turn
  
    //Turn

    //If we're close to a wall, then turn more abruptly
    if (center < FRONT_DISTANCE)
    {
      if (pos < 50)
        pos /= 3;
      if (pos > 50)
        pos *= 3;
    }

    int ms = map(pos, 0, 100, 90, 180);
    
    if (Debug)
    {
      Serial.print(center);
      Serial.print(",");
      Serial.print(left);
      Serial.print(",");
      Serial.print(right);
      Serial.print(",");
      Serial.println(ms);
    }
    
    //Serial.println(ms);
    steering.write(ms);

    //Driving speed
    int speed = 83;
    //if (center < CRASH_DISTANCE)
    //{
      //speed = 100; //reverse direction (90'ish is center)
      //car.ledOn();
    //}
    //else
    //{
      //car.ledOff();
    //}

    if (!MotorDisabled)
      motor.write(speed);
  }
  else if (startmodule_state == STOPPED)
  {
    motor.writeMicroseconds(1500);
    motor.detach();
    steering.detach();
    Serial.print("STOPPED");
    car.blinkLed(500);
  }
  else {
    Serial.print("Unknown startmodule state");
  }
  /*
  if (Serial.available())
  {
    int value = Serial.parseInt();
    motor.write(value);
    Serial.print("ESC set to ");
    Serial.println(value);
  }
  */

  //Serial.print("Elapsed us: ");
  //Serial.print(",");
  //Serial.println(elapsed);

  //Wait here so that each loop takes an exact amount of time.
  unsigned loopTime = 2000; //us
  while (elapsed < loopTime) {}
  elapsed = 0; 
  
}

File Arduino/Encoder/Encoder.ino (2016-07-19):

/*
 * Encoder - Photo Transistor
 */

int encoderPin = 17;
int ledPin = 13;

void setup()
{
  pinMode(encoderPin, INPUT);
  pinMode(ledPin, OUTPUT);
}

void loop()
{
  digitalWrite(ledPin, digitalRead(encoderPin));
}

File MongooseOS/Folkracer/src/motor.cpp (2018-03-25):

/*
 *
 */

#include "mgos.h"
#include "motor.hpp"

namespace Actuators {

    Motor::Motor(int pin) {
        this->_pin = pin;
    }

    //Fra CPP filen
    void Motor::setDesiredSpeed(float duty_cycle) {

        const int frequency = 50; //50Hz = 20ms

        //duty between 0 and 1.
        //float duty_cycle = 0.075f;
    
        //Servos typically need a PWM signal that is high somewhere between 1ms and 2ms. 
        //With a period of 20 ms, that means we get the following duty cycles:
        //1.0 ms = 0.05 duty cycle
        //1.5 ms = 0.075 duty cycle
        //2.0 ms = 0.1 duty cycle
        if (!mgos_pwm_set(_pin, frequency, duty_cycle))
        {
            LOG(LL_ERROR, ("Unable to set PWM for pin %d", _pin));
        }

        return;
    }

    void Motor::disable() {
        mgos_pwm_set(_pin, 0, 0);
    }
}

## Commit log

2016-05-27 Started on Schematic
    [Bluetooth.sch, FreeIMU.sch, Ghost.kicad_pcb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]
2016-05-28 Added IMU
    [Bluetooth.sch, FreeIMU.sch, Ghost.sch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]
2016-06-06 Lots of changes
    [Bluetooth.sch, FreeIMU.sch, Ghost.sch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]
2016-06-20 Fixed mounting holes.
    [Ghost-B.Cu.gbr, Ghost-B.Mask.gbr, Ghost-B.SilkS.gbr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]
2016-07-15 Started on Feature Tests in Arduino
    [Ghost.kicad_pcb]
2016-07-19 Some info, rev 1 printout, feature test code
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2016-07-31 Minor. Started on lasercut part.
    [PCB-top-plate.scad]
2016-08-04 Started on PCB rev 2
    [Bluetooth.sch, FreeIMU.sch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]
2016-08-04 Working on PCB layout for Rev 2
    [Ghost.kicad_pcb, Ghost.sch, IRSensors.sch]
2016-10-17 Added PCB mount
    [PCB-mount.scad]
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2016-10-25 PCB-mount lasercut
    [PCB-mount-v2.dxf, PCB-mount.dxf, PCB-mount.scad]
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2016-11-11 Playing around
    [SensorHolder1.scad]
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2016-11-12 Fixed steering compensation
2016-12-07 Replacing Teensy with ESP8266
    Changes made on KiCad on Ubuntu
    [Ghost.sch]
2016-12-07 Playing around with ROS and Gazebo
    [losi_car.sdf]
2016-12-09 Got a very basic world working
    [gothenburg.cfg]
2016-12-13 Minor changes
    [gothenburg.cfg]
2016-12-14 Simple robot
    [robot.yaml]
2017-01-29 Switching to ESP-WROOM-32
    [FreeIMU.sch, Ghost.sch, IRSensors.sch]
2017-02-01 Working on USB
    [USB.sch]
2017-02-01 More related to USB
    [FreeIMU.sch, Ghost.sch, IRSensors.sch]
2017-02-02 Created GhostESP32 shield schematics
    [GhostESP32.kicad_pcb, GhostESP32.sch]
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2017-02-04 Working on Steering for ESP32. Doesn't work yet.
    Maybe because the servo is 5V, but output from ESP is 3.3V?
    [main.c]
2017-02-05 Added Ghost Sensorboard schematics
    [FreeIMU.sch, GhostSensorboard.kicad_pcb, GhostSensorboard.sch]
2017-02-06 Started routing the GhostESP32 board
    [DP7043.dxf, GhostESP32.sch]
2017-02-07 Spent hours doing routing...
    [GhostESP32.kicad_pcb, GhostESP32.sch]
2017-02-13 Started on a lasercut sensorframe
    [SensorFrame.scad]
2017-02-21 GhostESP32 and GhostSensorboard mostly done - but with wrong 60 pin connector
    [FreeIMU.sch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]
2017-02-25 Routing finished. Playing around with BOM as XSL file.
    [FreeIMU.sch, GhostESP32.sch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]
2017-02-25 Both boards done, and sent to Elecrow.
    [FreeIMU.sch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]
2017-02-25 Working on the first simple ESP32 programs
    [GhostESP32-PTH.drl, GhostSensorboard-B.Cu.gbl, GhostSensorboard-B.Mask.gbs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]
2017-02-26 Comments about pins 34-39 and 6-11.
    [GhostESP32.sch]
2017-02-26 Trying to get button-to-led program to work. Doesn't yet.
    [main.c]
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2017-02-26 About to replace code
    [main.c]
2017-02-27 Startmodule connected to GPIO instead of 3V3 for software power recycle. Motor-pwm connected to IO25 instead of IO34 (which is input only) DRDY connected to IO33 instead of IO35 (which is input only)
    [FreeIMU.sch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]
2017-02-28 I2Cscanner works after adjusting timeout. Started on a TMP102 driver.
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2017-03-03 Eclipse is configured correctly
    [main.c]
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2017-03-09 Fixing sensorframe
    [SensorFrame.dxf, SensorFrame.scad, SensorFrame_WithHoles.dxf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]
2017-03-13 Several lasercut parts
    [EncoderDisc.scad, MiniSensorHolder.dxf, MiniSensorHolder.scad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]
2017-03-14 Started on Rev2 of Ghost PCBs
    [DP7043.dxf, FreeIMU.sch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]
2017-03-14 Made a connectorboard
    [FreeIMU.sch, GhostConnectorBoard.kicad_pcb, GhostConnectorBoard.sch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]
2017-03-16 Made encoder disc
    [EncoderDisc.dxf, EncoderDisc.scad]
2017-03-17 Working on the Encoder
    [GhostESP32.kicad_pcb, GhostESP32.sch, GhostSensorboard.kicad_pcb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]
2017-03-19 Ready to start routing. Schematics should be done.
    [GhostESP32.kicad_pcb, GhostESP32.sch, GhostSensorboard.kicad_pcb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]
2017-03-19 Ghost ESP32 done routing. Created Gerbers.
    [GhostESP32-B.Cu.gbr, GhostESP32-B.Mask.gbr, GhostESP32-B.Paste.gbr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]
2017-03-20 Rev2 sent to Elecrow for production
    [GhostESP32-B.Cu.gbl, GhostESP32-B.Mask.gbs, GhostESP32-B.Paste.gbp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]
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2017-04-07 Trying to get I2C to work, but it just crashes...
    [_saved_GhostESP32.sch]
2017-04-07 I2C scanner works
    [_saved_GhostESP32.sch]
2017-04-08 Working on getting the TCA9548 to work.
    [_saved_GhostESP32.sch]
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2017-04-13 Added empty project for C++
    [_saved_GhostESP32.sch]
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2017-04-30 TCA9548 has wrong footprint
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2017-05-06 Playing around with Wifi and sockets. Doesn't work
    [main.c]
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2017-05-28 Adding simple Boost example. Doesn't work.
    [main.c]
2017-05-30 Started on an experimental PCB
    [ExperimentVL53L0XMPU9250.kicad_pcb, ExperimentVL53L0XMPU9250.sch, mems.sch]
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2017-06-12 Working on Rev3 of the Ghost ESP32 schmatics
    [DP7043.dxf, GhostESP32.csv, GhostESP32.kicad_pcb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]
2017-06-17 Working on Rev3 of GhostESP32
    [GhostESP32-rev2.kicad_pcb, GhostESP32.kicad_pcb, GhostESP32.sch]
2017-06-17 Minors, probably autosaves
    [Rev2.kicad_pcb, Rev2.sch]
2017-06-17 Working on Rev3 of the sensorboard
    [FreeIMU.sch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]
2017-07-28 Unknown update
    [GhostESP32.kicad_pcb]
2017-07-28 Update to rev 3
    [GhostSensorboard.kicad_pcb, GhostSensorboard.sch, IRSensors.sch]
2017-07-28 Updated 3D models
    https://forum.kicad.info/t/incorrect-component-models-in-3d-viewer/7011/15
    [GhostSensorboard.kicad_pcb]
2017-08-11 Started on Rev 4 of the ESP32 PCB
    [GhostESP32.kicad_pcb, GhostESP32.sch, GhostSensorboard.sch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]
2018-02-05 A massive bunch of former changes waiting to be committed.
    [GhostESP32-2018-02-04-12-41-47.sch, GhostESP32-2018-02-05-22-23-16.sch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]
2018-02-07 Auto stash before merge of "master" and "origin/master"
    [GhostSensorboard-2018-02-07-21-29-52.sch, IRSensors-2018-02-07-21-29-52.sch, _saved_GhostSensorboard.sch]
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2018-02-09 Started on Rev5 of GhostESP32
    [GhostESP32-2018-02-04-12-41-47.sch, GhostESP32.kicad_pcb, GhostESP32.sch]
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2018-03-18 Working on revision 5 of the PCBs
    [GhostESP32-B.Cu.gbl, GhostESP32-B.Mask.gbs, GhostESP32-B.Paste.gbp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]
2018-03-18 Rev 5 of boards sent to production
    [GhostESP32-B.Cu.gbl, GhostESP32-B.Mask.gbs, GhostESP32-B.SilkS.gbo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]
2018-03-20 StartModule compiles
    But still problem inside goto_next_state method. The properties doesn't have a value.
    [main.cpp]
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2018-03-30 Started on tmp102 driver. Doesn't compile.
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2018-04-15 Calibration beeps correctly
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
